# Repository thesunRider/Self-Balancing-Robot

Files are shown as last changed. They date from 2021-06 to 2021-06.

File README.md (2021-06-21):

# Self Balancing Robot
#### This project does not use any stepper,This project works completely on BO DC motor

This is the most Simple Arduino based Simple Balancing Robot whose PID values were computed instead of the conventional hit and trial method, the gyro vs motor values were collected using HC-05 and fed to PID tuner to get exact PID values which were used in the project.

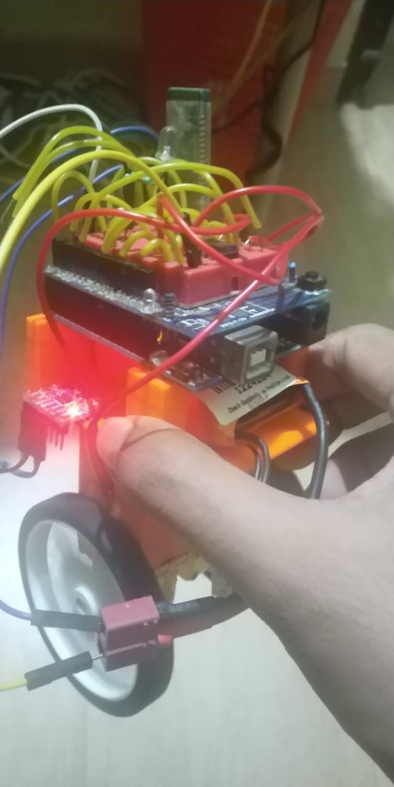
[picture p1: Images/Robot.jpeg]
bot


## Installation

3d Print the model chassis provided and mount the components\
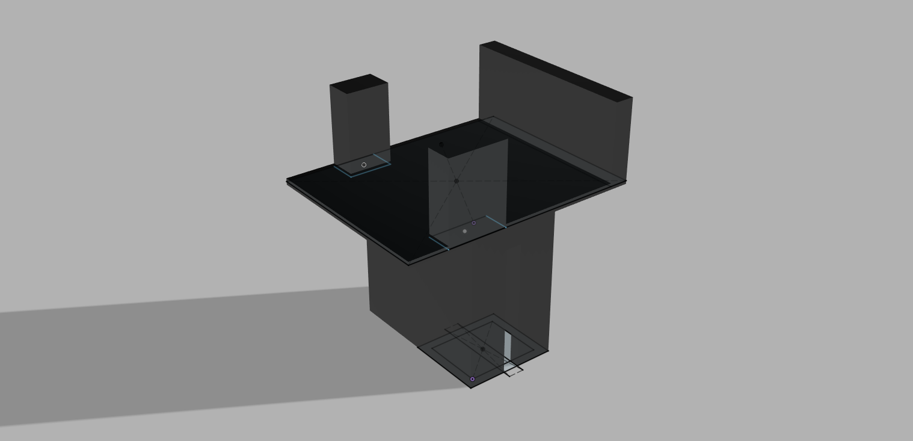
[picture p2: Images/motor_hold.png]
mount hold

#### if more stability is needed consider printing a taller mount so that the COM is high,the current COM model is close to the ground
Use the package manager of arduino to install Necessary libraries :

```bash
TinyMPU6050
AutoPID
Kalman 
L293D
```

## Usage

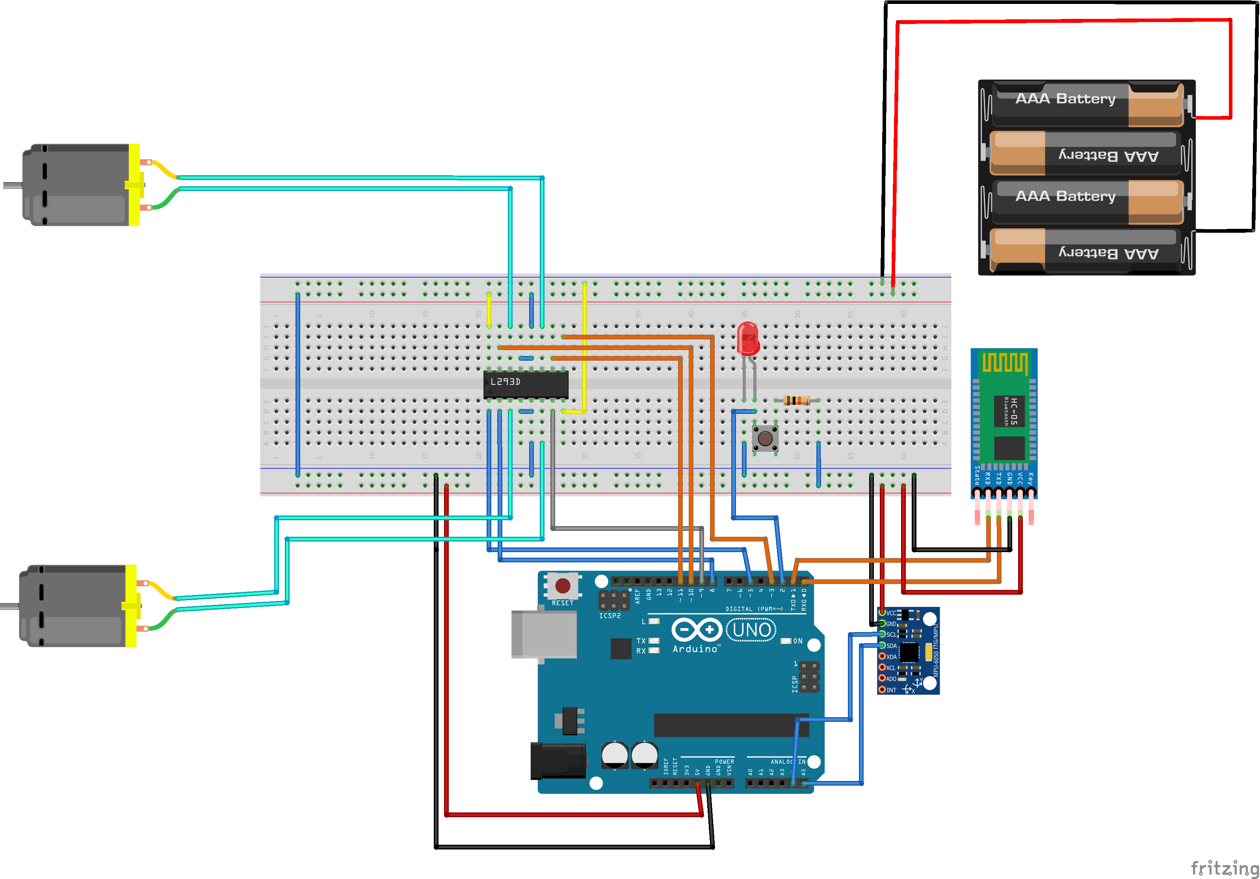
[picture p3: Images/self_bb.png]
Fritzing model fritzing project


Use motortester.ino to test Motor values and to find motor equalisation point ( the point at which both motors start to rotate) and add that offset. Set All pid's to zero.

Connect as per the circuit and Align the robot in a stable position and press the switch to record the angle which the robot should try to maintain. Now Record the data from HC-05 to a text file ,Now test the robot ,take the largest stablest oscillation readings,and discard the rest. Now feed the final text file to convert_piddata.ino to get a csv file which can be copy pasted to [pidtuner.com](pidtuner.com) to get PID values.

## Contributing
Pull requests are welcome. For major changes, please open an issue first to discuss what you would like to change.

Please make sure to update tests as appropriate.

## License
[MIT](https://choosealicense.com/licenses/mit/)

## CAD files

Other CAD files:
3dprint/motor_hold v5.f3d

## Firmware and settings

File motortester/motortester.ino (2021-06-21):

#include <L293D.h>
double motorsetcontrols(double control);
L293D motorL(3,11,10);
L293D motorR(5,9,8);
double control;
double inc = 0.1;
float i;
float k;
double inc_del = 0.025;

void setup()
{
  Serial.begin(9600);
}

void  loop()
{     
      for (int i = 0;i <= 10; i++){
      control = motorsetcontrols((double) i/20);
      motorL.set(control);
      motorR.set(control+inc_del);
      Serial.println(control);
      delay(1500);
      }
      for (int i = 0;i >= -10; i--){
      control = motorsetcontrols((double) i/20);
      motorL.set(control);
      motorR.set(control+inc_del);
      Serial.println(control);
      delay(1500);
      }
    
}

double motorsetcontrols(double control){
  Serial.println("dpping");
  control = control *10;
  if (control < 0){
    control = map(control,0,-10,-10,0);
    return control /10;
  }
  if (control > 0){
    return control/10;
  }
  
}

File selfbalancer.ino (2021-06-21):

//all includes available from arduino library manager
#include <Arduino.h>
#include <TinyMPU6050.h>
#include <AutoPID.h>
#include <Kalman.h> 
#include <L293D.h>



// CODE BY SURYASARADHI

double motorsetcontrols(double control);
#define READ_DELAY 1



//pid settings and gains  ,values from pidtuner website
#define KP 0.18
#define KI 1.85
#define KD 6400


//for eualising the power of both the motors
double inc_del = 0.025;

uint32_t timer;
double outputVal,controls;
double x_ang,y_ang,z_ang;
double kalAngleX, kalAngleY,kalAngleZ;


//Enable 3,5 
//control 11,10 - 9,8
L293D motorL(3,11,10);
L293D motorR(5,9,8);
double setPoint = 1.1,inputval = 1.5;
AutoPID selfPID(&inputval, &setPoint, &outputVal, -0.9, 0.9, KP, KI, KD);
Kalman kalmanX, kalmanY,kalmanZ;
MPU6050 mpu (Wire);

void switch_m(){
   motorL.set(0);
  motorR.set(0);
  Serial.println("switch set inpoint");
  mpu.Execute();
  x_ang = mpu.GetAngX();
  setPoint = x_ang;
  delay(1500);
}


/*
 *  Setup
 */
void setup() {

  Serial.begin(9600);
  pinMode(2,INPUT);
  mpu.Initialize();
  mpu.SetGyroOffsets(-675.29,57.50,-93.66);
  //mpu.Calibrate();
  
  mpu.Execute();
  
  kalmanX.setAngle(mpu.GetAngX()); 
  kalmanY.setAngle(mpu.GetAngY());
  kalmanZ.setAngle(mpu.GetAngY());

  selfPID.setBangBang(3); //when crossing 30 degrees set to full throttle to stabilize
  selfPID.setTimeStep(READ_DELAY); //set PID update interval to 10ms

  Serial.println("new==========");
}

/*
 *  Loop
 */
void loop() {
  mpu.Execute();
  x_ang = mpu.GetAngX();
  y_ang = mpu.GetAngY();
  z_ang = mpu.GetAngZ();
  if (digitalRead(2) == HIGH)
    switch_m();
  
  double dt = (double)(micros() - timer) / 1000000; // Calculate delta time
  timer = micros();

  kalAngleX = kalmanX.getAngle(x_ang, mpu.GetGyroX(), dt);
  kalAngleY = kalmanY.getAngle(y_ang, mpu.GetGyroY(), dt);
  kalAngleZ = kalmanZ.getAngle(z_ang, mpu.GetGyroZ(), dt);

  inputval = kalAngleX;
  
  
  selfPID.run();
  controls = motorsetcontrols(outputVal);
  motorL.set(controls);
  motorR.set(controls+inc_del);

  if (abs(inputval) > 15.0){
    Serial.println("ENDCONFIG");}
  else{
  Serial.print(inputval);
  Serial.print(",");
  Serial.print(controls);
  Serial.print(",");
  Serial.println(micros());
  }
  delay(READ_DELAY);
}


double motorsetcontrols(double control){
  control = control *10;
  if (control < 0){
    control = map(control,0,-10,-10,0);
    return control /10;
  }
  if (control > 0){
    return control/10;
  }
  
}

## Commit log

2021-06-21 Working PID based bot
2021-06-21 friting added
    [self.fzz]
2021-06-21 updated Readme and added Images
    [motor_hold v5.f3d]
